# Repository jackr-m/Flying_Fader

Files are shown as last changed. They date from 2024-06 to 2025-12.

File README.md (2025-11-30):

# Flying Faders
## Use Rust Embassy framework to integrate 5 "flying faders" (motorized linear slide potentiometers) as a USB MIDI CC controller

- [Flying Faders](#flying-faders)
   * [Use Rust Embassy framework to integrate 5 "flying faders" (motorized linear slide potentiometers) as a USB MIDI CC controller](#use-rust-embassy-framework-to-integrate-5-flying-faders-motorized-linear-slide-potentiometers-as-a-usb-midi-cc-controller)
   * [Project Overview](#project-overview)
      + [Code](#code)
      + [Mechanical](#mechanical)

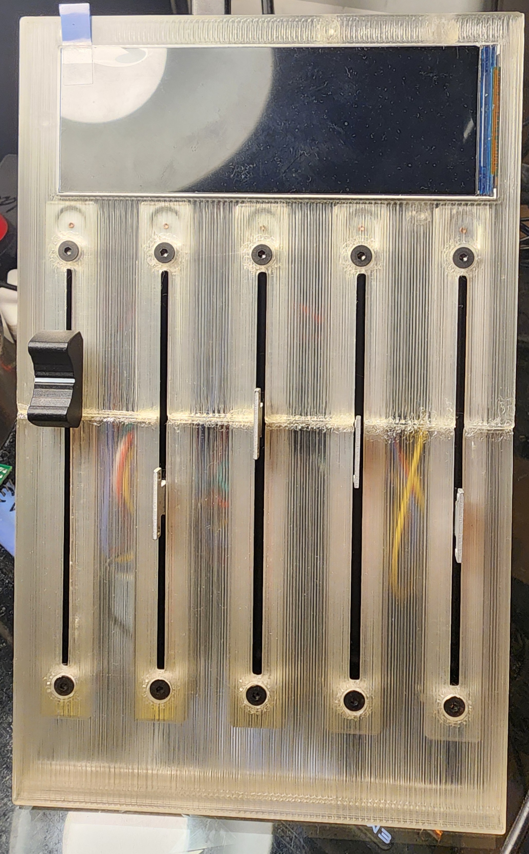
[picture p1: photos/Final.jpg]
Final product


## Project Overview
Use 5 motorized linear slide potentiometers (ALPS SM10002NKA1X-HW1, sold as Adafruit P/N 5466) with a STM32H7 microprocessor programmed using the Rust Embassy framework & HAL.
There is a custom PCB for this project, with the KiCad source in the /CAD directory.
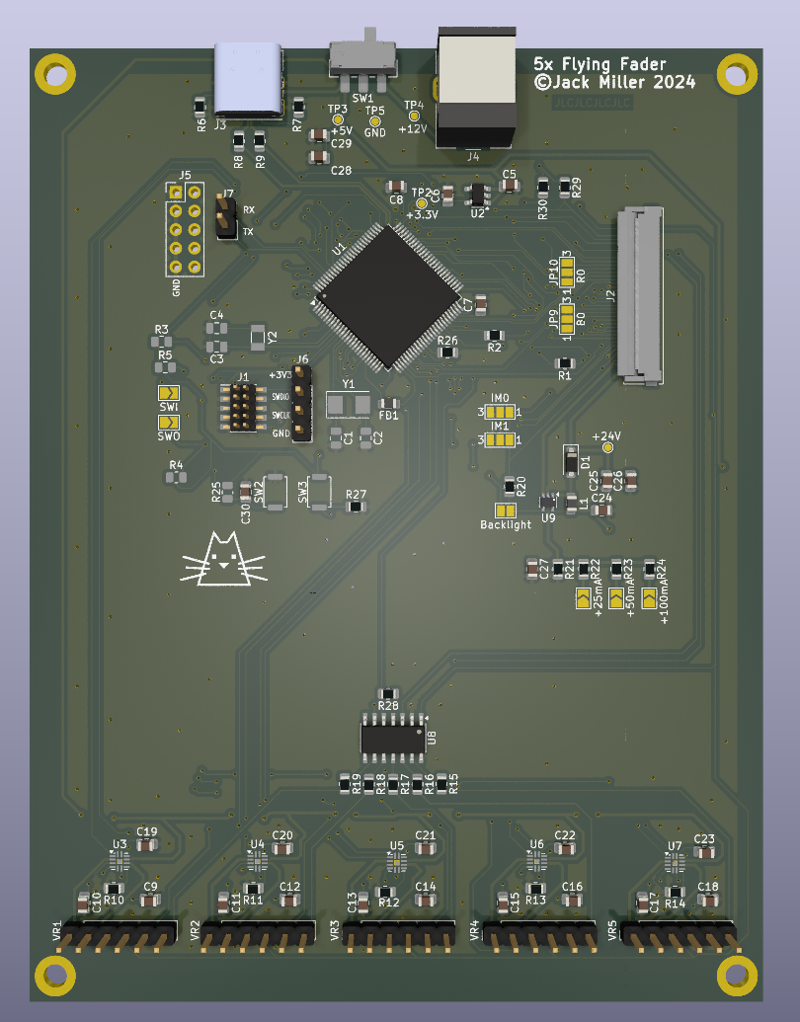
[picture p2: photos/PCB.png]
PCB


### Code
Using the Rust Embassy framework and embassy_stm32 HAL, this has been coded using an asynchronous architecture and should be very portable to nearly any STM32 variant (especially if the screen is not needed).
Code documentation located at: https://jackr-m.github.io/Flying_Fader/flying_fader/

### Mechanical
The casement is 3D printed, and STEP files are provided in the /CAD directory.
In addition, the original Onshape document is available for use or modification at [Onshape](https://cad.onshape.com/documents/5790ae0e6f82956a005dc546/w/d37346e9ef2c1592c912aa6b/e/dacfcc9dc0c38682bf8baa7f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).
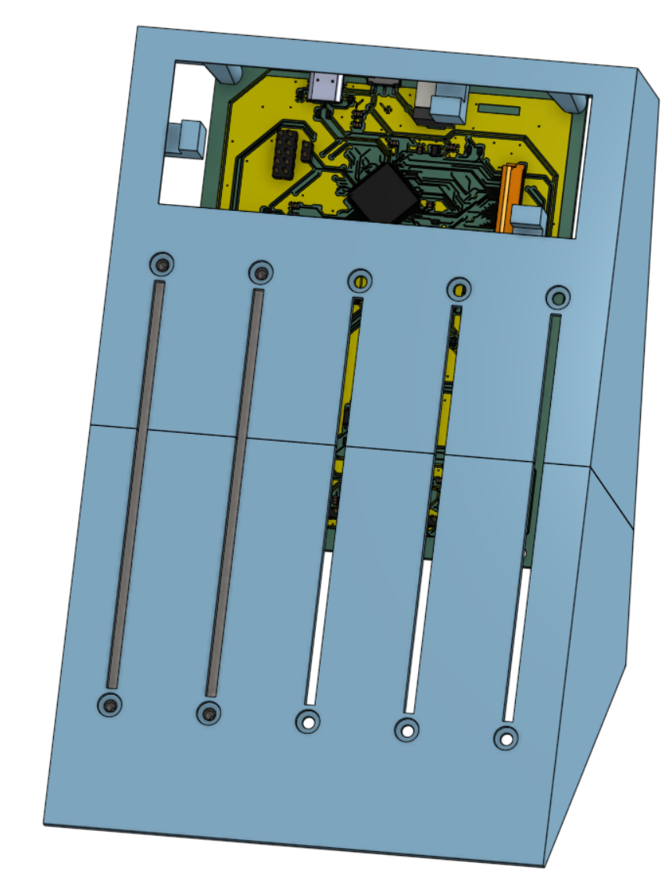
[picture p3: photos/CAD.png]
CAD


Faders:
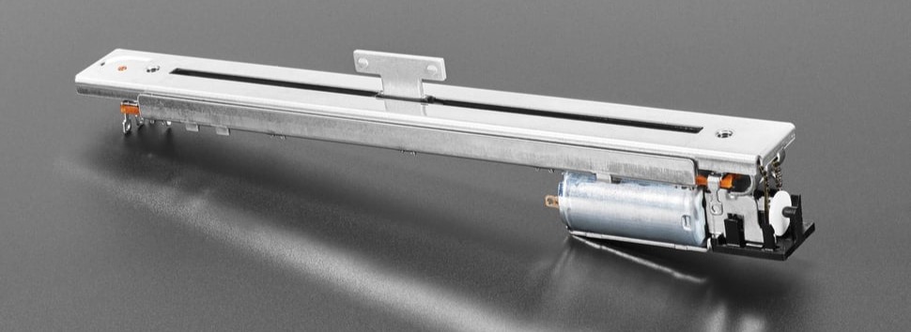
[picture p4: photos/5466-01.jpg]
Fader

https://www.adafruit.com/product/5466

Screen:
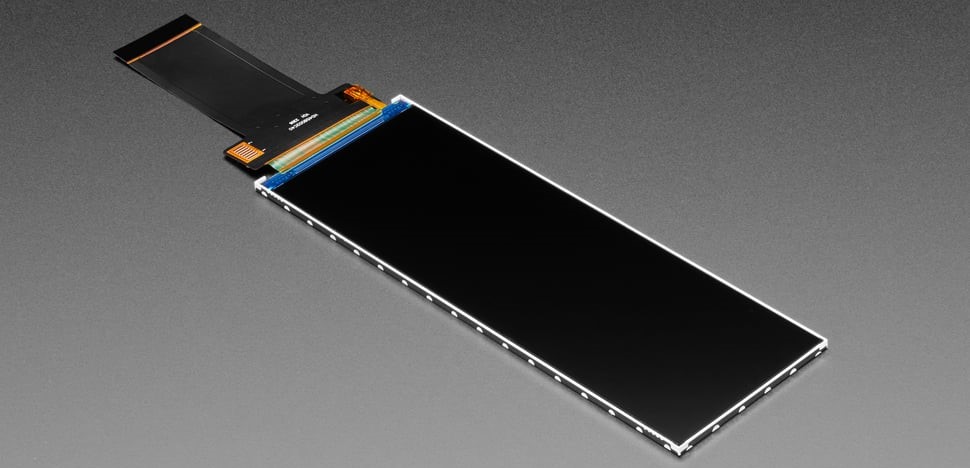
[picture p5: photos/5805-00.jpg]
Screem

https://www.adafruit.com/product/5805

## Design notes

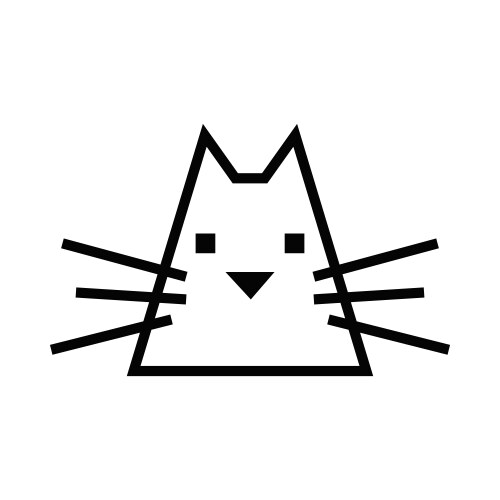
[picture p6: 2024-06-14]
CAD/cat.jpg

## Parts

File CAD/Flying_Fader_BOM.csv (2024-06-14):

Reference | Value | Datasheet | Footprint | Qty | DNP
C1,C2,C3,C4 | C_Small | ~ | Capacitor_SMD:C_0805_2012Metric | 4 | DNP
C5,C6,C25,C26 | 1u | ~ | Capacitor_SMD:C_0805_2012Metric | 4
C7,C8 | 2.2u | ~ | Capacitor_SMD:C_0805_2012Metric | 2
C9,C12,C14,C16,C18,C27,C28,C30 | 0.1u | ~ | Capacitor_SMD:C_0805_2012Metric | 8
C10,C11,C13,C15,C17 | 0.47u | ~ | Capacitor_SMD:C_0805_2012Metric | 5
C19,C20,C21,C22,C23 | 0.1n | ~ | Capacitor_SMD:C_0805_2012Metric | 5
C24,C29 | 10u | ~ | Capacitor_SMD:C_0805_2012Metric | 2
D1 | MBR0540 | http://www.mccsemi.com/up_pdf/MBR0520~MBR0580(SOD123).pdf | Diode_SMD:D_SOD-123 | 1
FB1 | 10uH | ~ | Inductor_SMD:L_0805_2012Metric | 1
J1 | Conn_ARM_JTAG_SWD_10 | http://infocenter.arm.com/help/topic/com.arm.doc.ddi0314h/DDI0314H_coresight_components_trm.pdf | Connector_PinHeader_1.27mm:PinHeader_2x05_P1.27mm_Vertical_SMD | 1
J2 | 40P_FPC_0.5mm | ~ | Connector_FFC-FPC:Omron_XF2M-4015-1A_1x40-1MP_P0.5mm_Horizontal | 1
J3 | USB_C_Receptacle_USB2.0_16P | https://www.usb.org/sites/default/files/documents/usb_type-c.zip | Connector_USB:USB_C_Receptacle_GCT_USB4085 | 1
J4 | Barrel_Jack | ~ | Connector_BarrelJack:BarrelJack_CUI_PJ-063AH_Horizontal | 1
J5 | Conn_02x05_Odd_Even | ~ | Connector_PinHeader_2.54mm:PinHeader_2x05_P2.54mm_Vertical | 1
J6 | Conn_01x04_Pin | ~ | Connector_PinHeader_2.54mm:PinHeader_1x04_P2.54mm_Vertical | 1
J7 | UART4 | ~ | Connector_PinHeader_2.54mm:PinHeader_1x02_P2.54mm_Vertical | 1
L1 | 6.8u | ~ | Inductor_SMD:L_0805_2012Metric | 1
R1,R15,R16,R17,R18,R19,R20,R26,R27 | 10k | ~ | Resistor_SMD:R_0805_2012Metric | 9
R2 | 100 | ~ | Resistor_SMD:R_0805_2012Metric | 1
R3,R4,R5,R25 | 10k | ~ | Resistor_SMD:R_0805_2012Metric | 4 | DNP
R6,R7 | 5.1k | ~ | Resistor_SMD:R_0805_2012Metric | 2
R8,R9 | 0 | ~ | Resistor_SMD:R_0805_2012Metric | 2
R10,R11,R12,R13,R14 | 6.8k | ~ | Resistor_SMD:R_0805_2012Metric | 5
R21,R22 | 8.2 | ~ | Resistor_SMD:R_0805_2012Metric | 2
R23 | 4.3 | ~ | Resistor_SMD:R_0805_2012Metric | 1
R24 | 2 | ~ | Resistor_SMD:R_0805_2012Metric | 1
R28,R29,R30 | 4.7k | ~ | Resistor_SMD:R_0805_2012Metric | 3
SW1 | SW_SPDT | ~ | Button_Switch_SMD:SW_SPDT_CK_JS102011SAQN | 1
SW2 | RESET | ~ | Button_Switch_SMD:SW_Push_SPST_NO_Alps_SKRK | 1
SW3 | BOOT0 | ~ | Button_Switch_SMD:SW_Push_SPST_NO_Alps_SKRK | 1
TP1 | +24V | ~ | TestPoint:TestPoint_Pad_D1.0mm | 1
TP2 | +3.3V | ~ | TestPoint:TestPoint_Pad_D1.0mm | 1
TP3 | +5V | ~ | TestPoint:TestPoint_Pad_D1.0mm | 1
TP4 | +12V | ~ | TestPoint:TestPoint_Pad_D1.0mm | 1
TP5 | GND | ~ | TestPoint:TestPoint_Pad_D1.0mm | 1
U1 | STM32H7A3VITx | https://www.st.com/resource/en/datasheet/stm32h7a3vi.pdf | Package_QFP:LQFP-100_14x14mm_P0.5mm | 1
U2 | MIC5504-3.3YM5 | http://ww1.microchip.com/downloads/en/DeviceDoc/MIC550X.pdf | Package_TO_SOT_SMD:SOT-23-5 | 1
U3,U4,U5,U6,U7 | MP6550GG-Z | MP6550GG-Z | Package_DFN_QFN:LQFN-12-1EP_2x2mm_P0.5mm_EP0.7x0.7mm | 5
U8 | AT42QT1070-S | http://ww1.microchip.com/downloads/en/DeviceDoc/Atmel-9596-AT42-QTouch-BSW-AT42QT1070_Datasheet.pdf | Package_SO:SOIC-14_3.9x8.7mm_P1.27mm | 1
U9 | TPS61169DCKR |  | Package_TO_SOT_SMD:SOT-353_SC-70-5 | 1
VR1,VR2,VR3,VR4,VR5 | SM10002NKA1X-HW1 | https://cdn-shop.adafruit.com/product-files/5466/5466_datasheetSM10001.pdf | Connector_PinHeader_2.54mm:PinHeader_1x06_P2.54mm_Vertical | 5
Y1 | 50MHz | ~ | Crystal:Crystal_SMD_5032-2Pin_5.0x3.2mm | 1 | DNP
Y2 | 32.768kHz | ~ | Crystal:Crystal_SMD_3215-2Pin_3.2x1.5mm | 1 | DNP

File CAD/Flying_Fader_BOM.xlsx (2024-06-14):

Reference | Value | Datasheet | Footprint | Qty | DNP | DigiKey P/N
C1,C2,C3,C4 | C_Small | ~ | Capacitor_SMD:C_0805_2012Metric | 4 | DNP | --
C5,C6,C25,C26 | 1u | ~ | Capacitor_SMD:C_0805_2012Metric | 4 |  | 0805 Book
C7,C8 | 2.2u | ~ | Capacitor_SMD:C_0805_2012Metric | 2 |  | 445-CGA4J1X7R2A225K125ACCT-ND
C9,C12,C14,C16,C18,C27,C28,C30 | 0.1u | ~ | Capacitor_SMD:C_0805_2012Metric | 8 |  | 0805 Book
C10,C11,C13,C15,C17 | 0.47u | ~ | Capacitor_SMD:C_0805_2012Metric | 5 |  | 0805 Book
C19,C20,C21,C22,C23 | 0.1n | ~ | Capacitor_SMD:C_0805_2012Metric | 5 |  | 0805 Book
C24,C29 | 10u | ~ | Capacitor_SMD:C_0805_2012Metric | 2 |  | 490-GRJ21BR61E106KE01KCT-ND
D1 | MBR0540 | http://www.mccsemi.com/up_pdf/MBR0520~MBR0580(SOD123).pdf | Diode_SMD:D_SOD-123 | 1 |  | 1655-MBR0540CT-ND
FB1 | 10uH | ~ | Inductor_SMD:L_0805_2012Metric | 1 |  | 553-2392-1-ND
J1 | Conn_ARM_JTAG_SWD_10 | http://infocenter.arm.com/help/topic/com.arm.doc.ddi0314h/DDI0314H_coresight_components_trm.pdf | Connector_PinHeader_1.27mm:PinHeader_2x05_P1.27mm_Vertical_SMD | 1 | DNP | --
J2 | 40P_FPC_0.5mm | ~ | Connector_FFC-FPC:Omron_XF2M-4015-1A_1x40-1MP_P0.5mm_Horizontal | 1 |  | OR729CT-ND
J3 | USB_C_Receptacle_USB2.0_16P | https://www.usb.org/sites/default/files/documents/usb_type-c.zip | Connector_USB:USB_C_Receptacle_GCT_USB4085 | 1 |  | 2073-USB4085-GF-ACT-ND
J4 | Barrel_Jack | ~ | Connector_BarrelJack:BarrelJack_CUI_PJ-063AH_Horizontal | 1 |  | CP-063AH-ND
J5 | Conn_02x05_Odd_Even | ~ | Connector_PinHeader_2.54mm:PinHeader_2x05_P2.54mm_Vertical | 1 | DNP
J6 | Conn_01x04_Pin | ~ | Connector_PinHeader_2.54mm:PinHeader_1x04_P2.54mm_Vertical | 1 |  | --
J7 | UART4 | ~ | Connector_PinHeader_2.54mm:PinHeader_1x02_P2.54mm_Vertical | 1 |  | --
L1 | 6.8u | ~ | Inductor_SMD:L_0805_2012Metric | 1 |  | 445-6761-1-ND
R1,R15,R16,R17,R18,R19,R20,R26,R27 | 10k | ~ | Resistor_SMD:R_0805_2012Metric | 9 |  | 0805 Book
R2 | 100 | ~ | Resistor_SMD:R_0805_2012Metric | 1 |  | 0805 Book
R3,R4,R5,R25 | 10k | ~ | Resistor_SMD:R_0805_2012Metric | 4 | DNP | 0805 Book
R6,R7 | 5.1k | ~ | Resistor_SMD:R_0805_2012Metric | 2 |  | 0805 Book
R8,R9 | 0 | ~ | Resistor_SMD:R_0805_2012Metric | 2 |  | 0805 Book
R10,R11,R12,R13,R14 | 6.8k | ~ | Resistor_SMD:R_0805_2012Metric | 5 |  | 0805 Book
R21,R22 | 8.2 | ~ | Resistor_SMD:R_0805_2012Metric | 2 |  | 0805 Book
R23 | 4.3 | ~ | Resistor_SMD:R_0805_2012Metric | 1 |  | 0805 Book
R24 | 2 | ~ | Resistor_SMD:R_0805_2012Metric | 1 |  | 0805 Book
R28,R29,R30 | 4.7k | ~ | Resistor_SMD:R_0805_2012Metric | 3 |  | 311-4.7KARCT-ND
SW1 | SW_SPDT | ~ | Button_Switch_SMD:SW_SPDT_CK_JS102011SAQN | 1 |  | 401-1999-1-ND
SW2 | RESET | ~ | Button_Switch_SMD:SW_Push_SPST_NO_Alps_SKRK | 1 |  | 4809-SKRKAHE020CT-ND
SW3 | BOOT0 | ~ | Button_Switch_SMD:SW_Push_SPST_NO_Alps_SKRK | 1 |  | 4809-SKRKAHE020CT-ND
TP1 | +24V | ~ | TestPoint:TestPoint_Pad_D1.0mm | 1 |  | --
TP2 | +3.3V | ~ | TestPoint:TestPoint_Pad_D1.0mm | 1 |  | --
TP3 | +5V | ~ | TestPoint:TestPoint_Pad_D1.0mm | 1 |  | --
TP4 | +12V | ~ | TestPoint:TestPoint_Pad_D1.0mm | 1 |  | --
TP5 | GND | ~ | TestPoint:TestPoint_Pad_D1.0mm | 1 |  | --
U1 | STM32H7A3VITx | https://www.st.com/resource/en/datasheet/stm32h7a3vi.pdf | Package_QFP:LQFP-100_14x14mm_P0.5mm | 1 |  | 497-STM32H7A3VIT6-ND
U2 | MIC5504-3.3YM5 | http://ww1.microchip.com/downloads/en/DeviceDoc/MIC550X.pdf | Package_TO_SOT_SMD:SOT-23-5 | 1 |  | 576-4764-1-ND
U3,U4,U5,U6,U7 | MP6550GG-Z | MP6550GG-Z | Package_DFN_QFN:LQFN-12-1EP_2x2mm_P0.5mm_EP0.7x0.7mm | 5 |  | 1589-MP6550GG-ZCT-ND
U8 | AT42QT1070-S | http://ww1.microchip.com/downloads/en/DeviceDoc/Atmel-9596-AT42-QTouch-BSW-AT42QT1070_Datasheet.pdf | Package_SO:SOIC-14_3.9x8.7mm_P1.27mm | 1 |  | AT42QT1070-SSURCT-ND
U9 | TPS61169DCKR |  | Package_TO_SOT_SMD:SOT-353_SC-70-5 | 1 |  | 296-40821-1-ND
VR1,VR2,VR3,VR4,VR5 | SM10002NKA1X-HW1 | https://cdn-shop.adafruit.com/product-files/5466/5466_datasheetSM10001.pdf | Connector_PinHeader_2.54mm:PinHeader_1x06_P2.54mm_Vertical | 5 |  | 1528-5466-ND | 1528-5741-ND
Y1 | 50MHz | ~ | Crystal:Crystal_SMD_5032-2Pin_5.0x3.2mm | 1 | DNP | 50-ECS-500-CDX-2166CT-ND
Y2 | 32.768kHz | ~ | Crystal:Crystal_SMD_3215-2Pin_3.2x1.5mm | 1 | DNP | 50-ECS-.327-6-34B-C-CT-ND

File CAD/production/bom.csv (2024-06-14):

Designator | Footprint | Quantity | Value | LCSC Part #
C1, C2, C3, C4 | 0805 | 4 | C_Small
C10, C11, C13, C15, C17 | 0805 | 5 | 0.47u
C12, C14, C16, C18, C27, C28, C30, C9 | 0805 | 8 | 0.1u
C19, C20, C21, C22, C23 | 0805 | 5 | 0.1n
C24, C29 | 0805 | 2 | 10u
C25, C26, C5, C6 | 0805 | 4 | 1u
C7, C8 | 0805 | 2 | 2.2u
D1 | D_SOD-123 | 1 | MBR0540
FB1 | 0805 | 1 | 10uH
J1 | PinHeader_2x05_P1.27mm_Vertical_SMD | 1 | Conn_ARM_JTAG_SWD_10
J2 | Omron_XF2M-4015-1A_1x40-1MP_P0.5mm_Horizontal | 1 | 40P_FPC_0.5mm
J3 | USB_C_Receptacle_GCT_USB4085 | 1 | USB_C_Receptacle_USB2.0_16P
J4 | BarrelJack_CUI_PJ-063AH_Horizontal | 1 | Barrel_Jack
J5 | PinHeader_2x05_P2.54mm_Vertical | 1 | Conn_02x05_Odd_Even
J6 | PinHeader_1x04_P2.54mm_Vertical | 1 | Conn_01x04_Pin
J7 | PinHeader_1x02_P2.54mm_Vertical | 1 | UART4
L1 | 0805 | 1 | 6.8u
R1, R15, R16, R17, R18, R19, R20, R25, R26, R27, R3, R4, R5 | 0805 | 13 | 10k
R10, R11, R12, R13, R14 | 0805 | 5 | 6.8k
R2 | 0805 | 1 | 100
R21, R22 | 0805 | 2 | 8.2
R23 | 0805 | 1 | 4.3
R24 | 0805 | 1 | 2
R28, R29, R30 | 0805 | 3 | 4.7k
R6, R7 | 0805 | 2 | 5.1k
R8, R9 | 0805 | 2 | 0
SW1 | SW_SPDT_CK_JS102011SAQN | 1 | SW_SPDT
SW2 | SW_Push_SPST_NO_Alps_SKRK | 1 | RESET
SW3 | SW_Push_SPST_NO_Alps_SKRK | 1 | BOOT0
TP1 | TestPoint_Pad_D1.0mm | 1 | +24V
TP2 | TestPoint_Pad_D1.0mm | 1 | +3.3V
TP3 | TestPoint_Pad_D1.0mm | 1 | +5V
TP4 | TestPoint_Pad_D1.0mm | 1 | +12V
TP5 | TestPoint_Pad_D1.0mm | 1 | GND
U1 | LQFP-100_14x14mm_P0.5mm | 1 | STM32H7A3VITx
U2 | SOT-23-5 | 1 | MIC5504-3.3YM5
U3, U4, U5, U6, U7 | LQFN-12-1EP_2x2mm_P0.5mm_EP0.7x0.7mm | 5 | MP6550GG-Z
U8 | SOIC-14_3.9x8.7mm_P1.27mm | 1 | AT42QT1070-S
U9 | SOT-353_SC-70-5 | 1 | TPS61169DCKR
VR1, VR2, VR3, VR4, VR5 | PinHeader_1x06_P2.54mm_Vertical | 5 | SM10002NKA1X-HW1
Y1 | Crystal_SMD_5032-2Pin_5.0x3.2mm | 1 | 50MHz
Y2 | Crystal_SMD_3215-2Pin_3.2x1.5mm | 1 | 32.768kHz

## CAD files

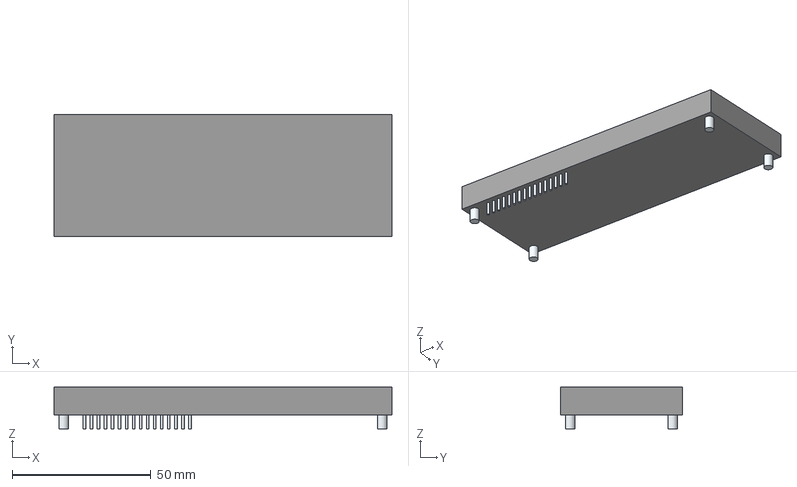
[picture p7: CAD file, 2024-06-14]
CAD/LIB_NHD-0216SZW-BG5/NHD-0216SZW-BG5/3D/NHD-0216SZW-BG5.stp
122.0 x 44.0 x 15.1 mm
Leads x 20

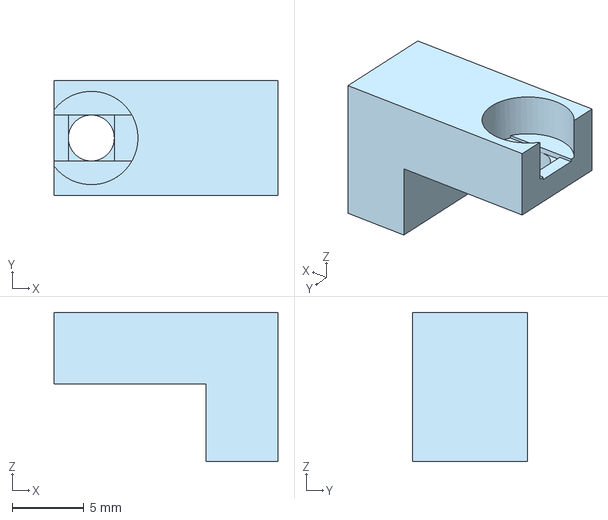
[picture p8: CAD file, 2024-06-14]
CAD/Screen Clamp Short.step
15.6 x 8.00 x 10.4 mm

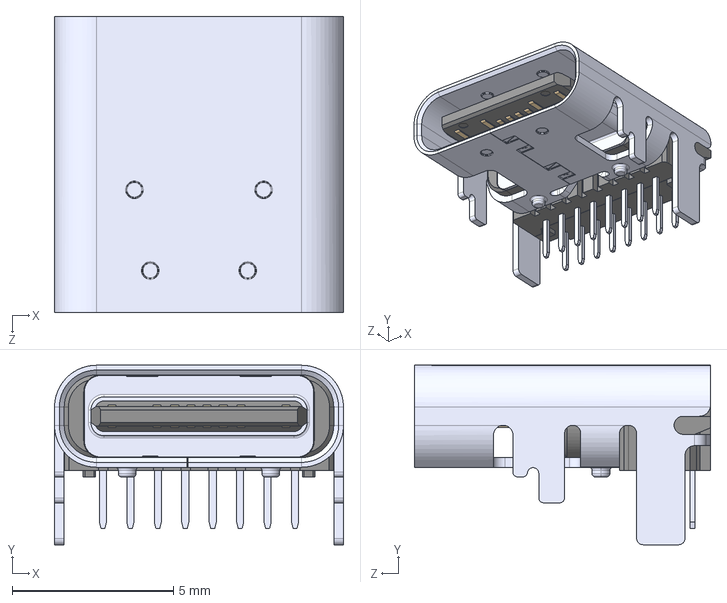
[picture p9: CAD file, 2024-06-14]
CAD/USB4085_GF_A/USB4085-GF-A.step
8.95 x 5.56 x 9.17 mm

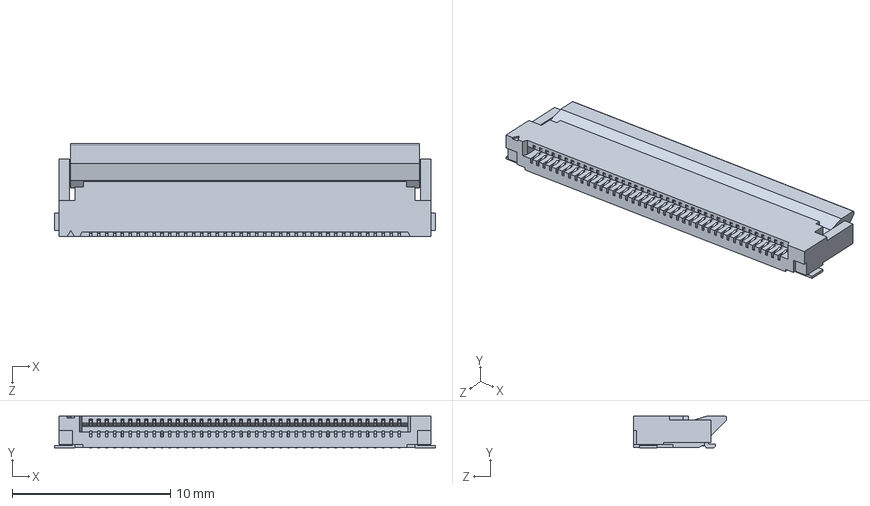
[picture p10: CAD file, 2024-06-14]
CAD/XF2M_4015_1A/XF2M_4015_1A.step
24.1 x 2.00 x 5.90 mm

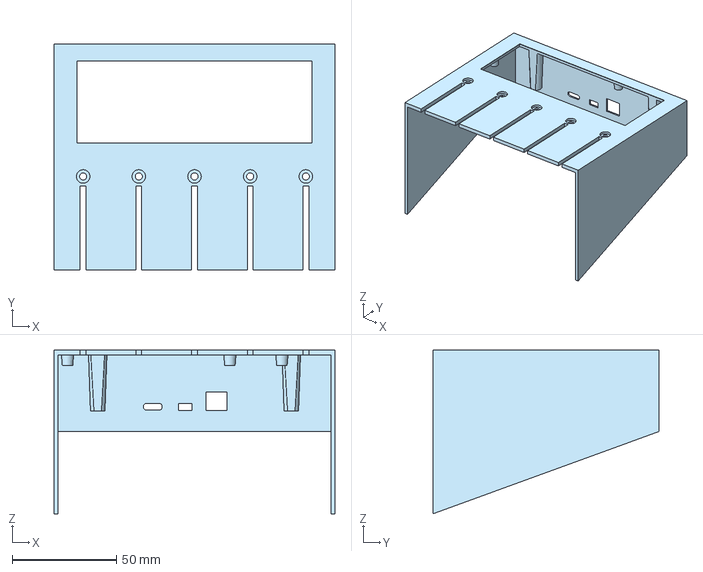
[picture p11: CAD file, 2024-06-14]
CAD/Top Panel Upper.step
135.0 x 108.6 x 78.6 mm

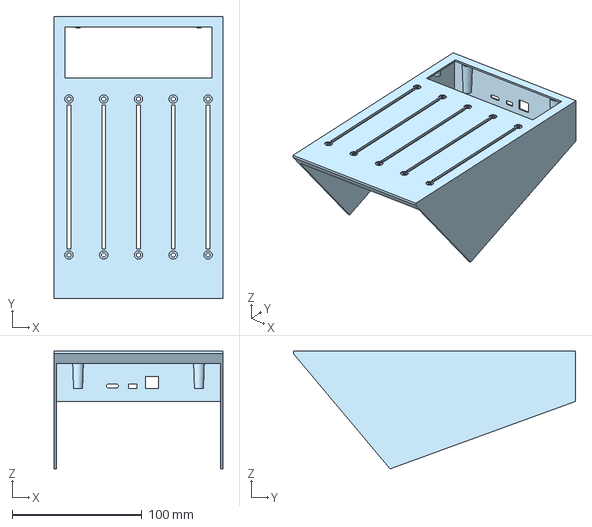
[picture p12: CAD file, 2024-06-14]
CAD/Top Panel.step
130.0 x 217.0 x 90.6 mm

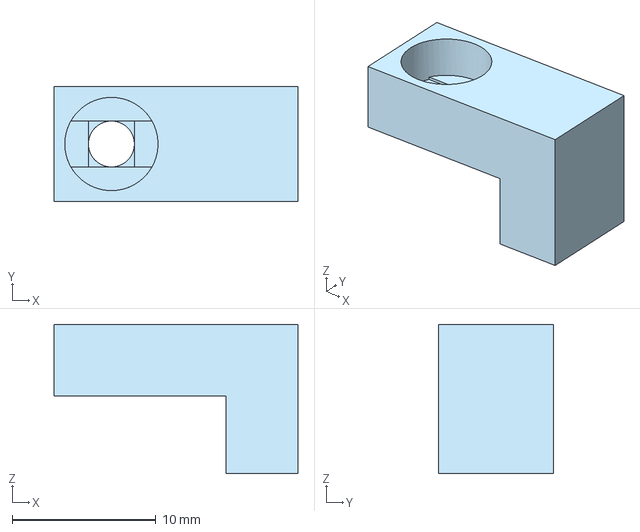
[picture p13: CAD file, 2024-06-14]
CAD/Screen Clamp.step
17.0 x 8.00 x 10.4 mm

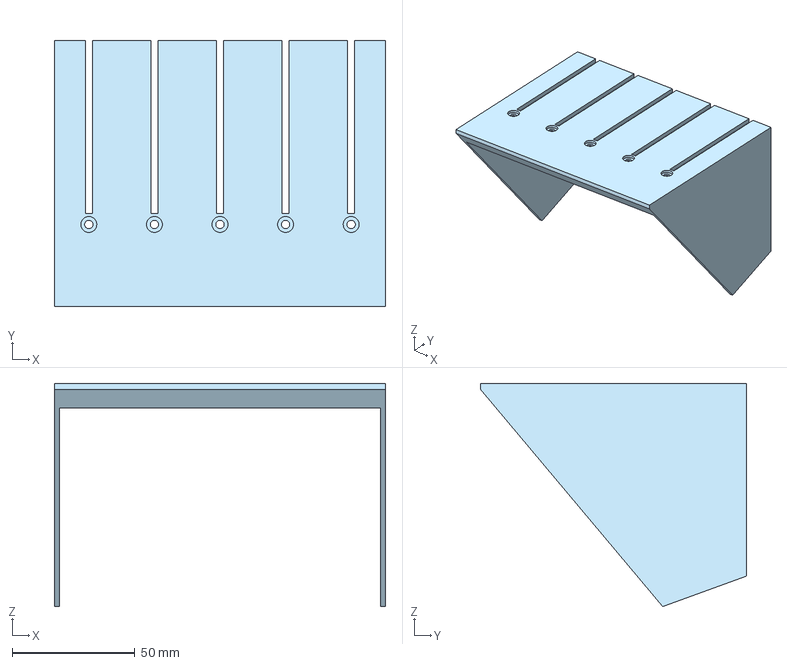
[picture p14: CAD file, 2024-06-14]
CAD/Top Panel Lower.step
135.0 x 108.6 x 91.0 mm

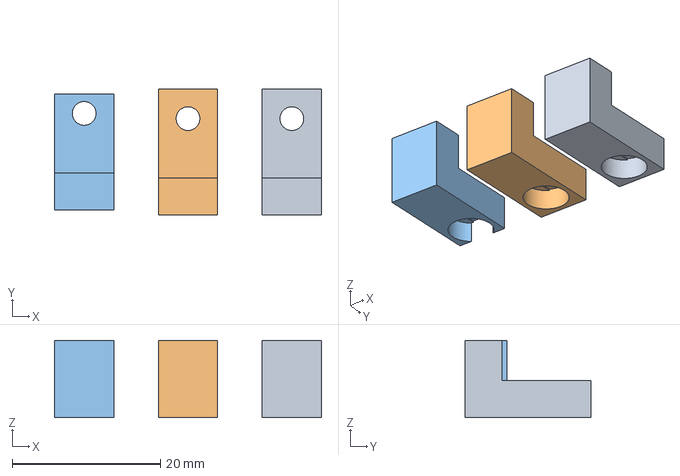
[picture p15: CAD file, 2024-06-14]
CAD/Screen Clamps.3mf
36.0 x 17.0 x 10.4 mm
Screen Clamp
Screen Clamp Short

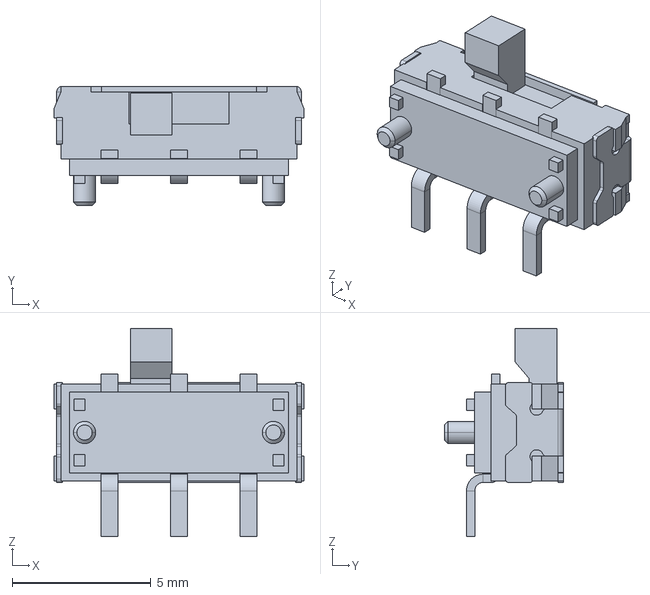
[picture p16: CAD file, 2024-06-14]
CAD/JS102011SAQN/JS102011SAQN.step
9.00 x 4.30 x 7.50 mm

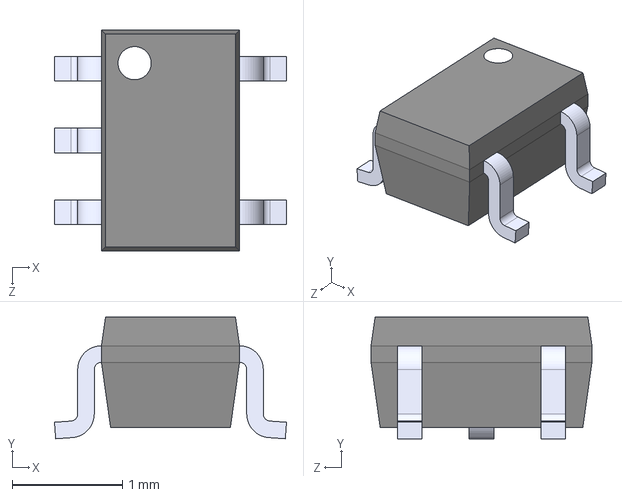
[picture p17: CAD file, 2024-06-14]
CAD/TPS61169DCKR/TPS61169DCKR.step
2.10 x 1.10 x 2.00 mm

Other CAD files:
CAD/LIB_NHD-0216SZW-BG5/NHD-0216SZW-BG5/Allegro/nhd0216szwbg5.psm
CAD/LIB_NHD-0216SZW-BG5/NHD-0216SZW-BG5/DEHDL/nhd_0216szw_bg5/chips/chips.prt
CAD/Top Panel Lower.3mf
CAD/Top Panel Upper.3mf
CAD/Top Panel.3mf

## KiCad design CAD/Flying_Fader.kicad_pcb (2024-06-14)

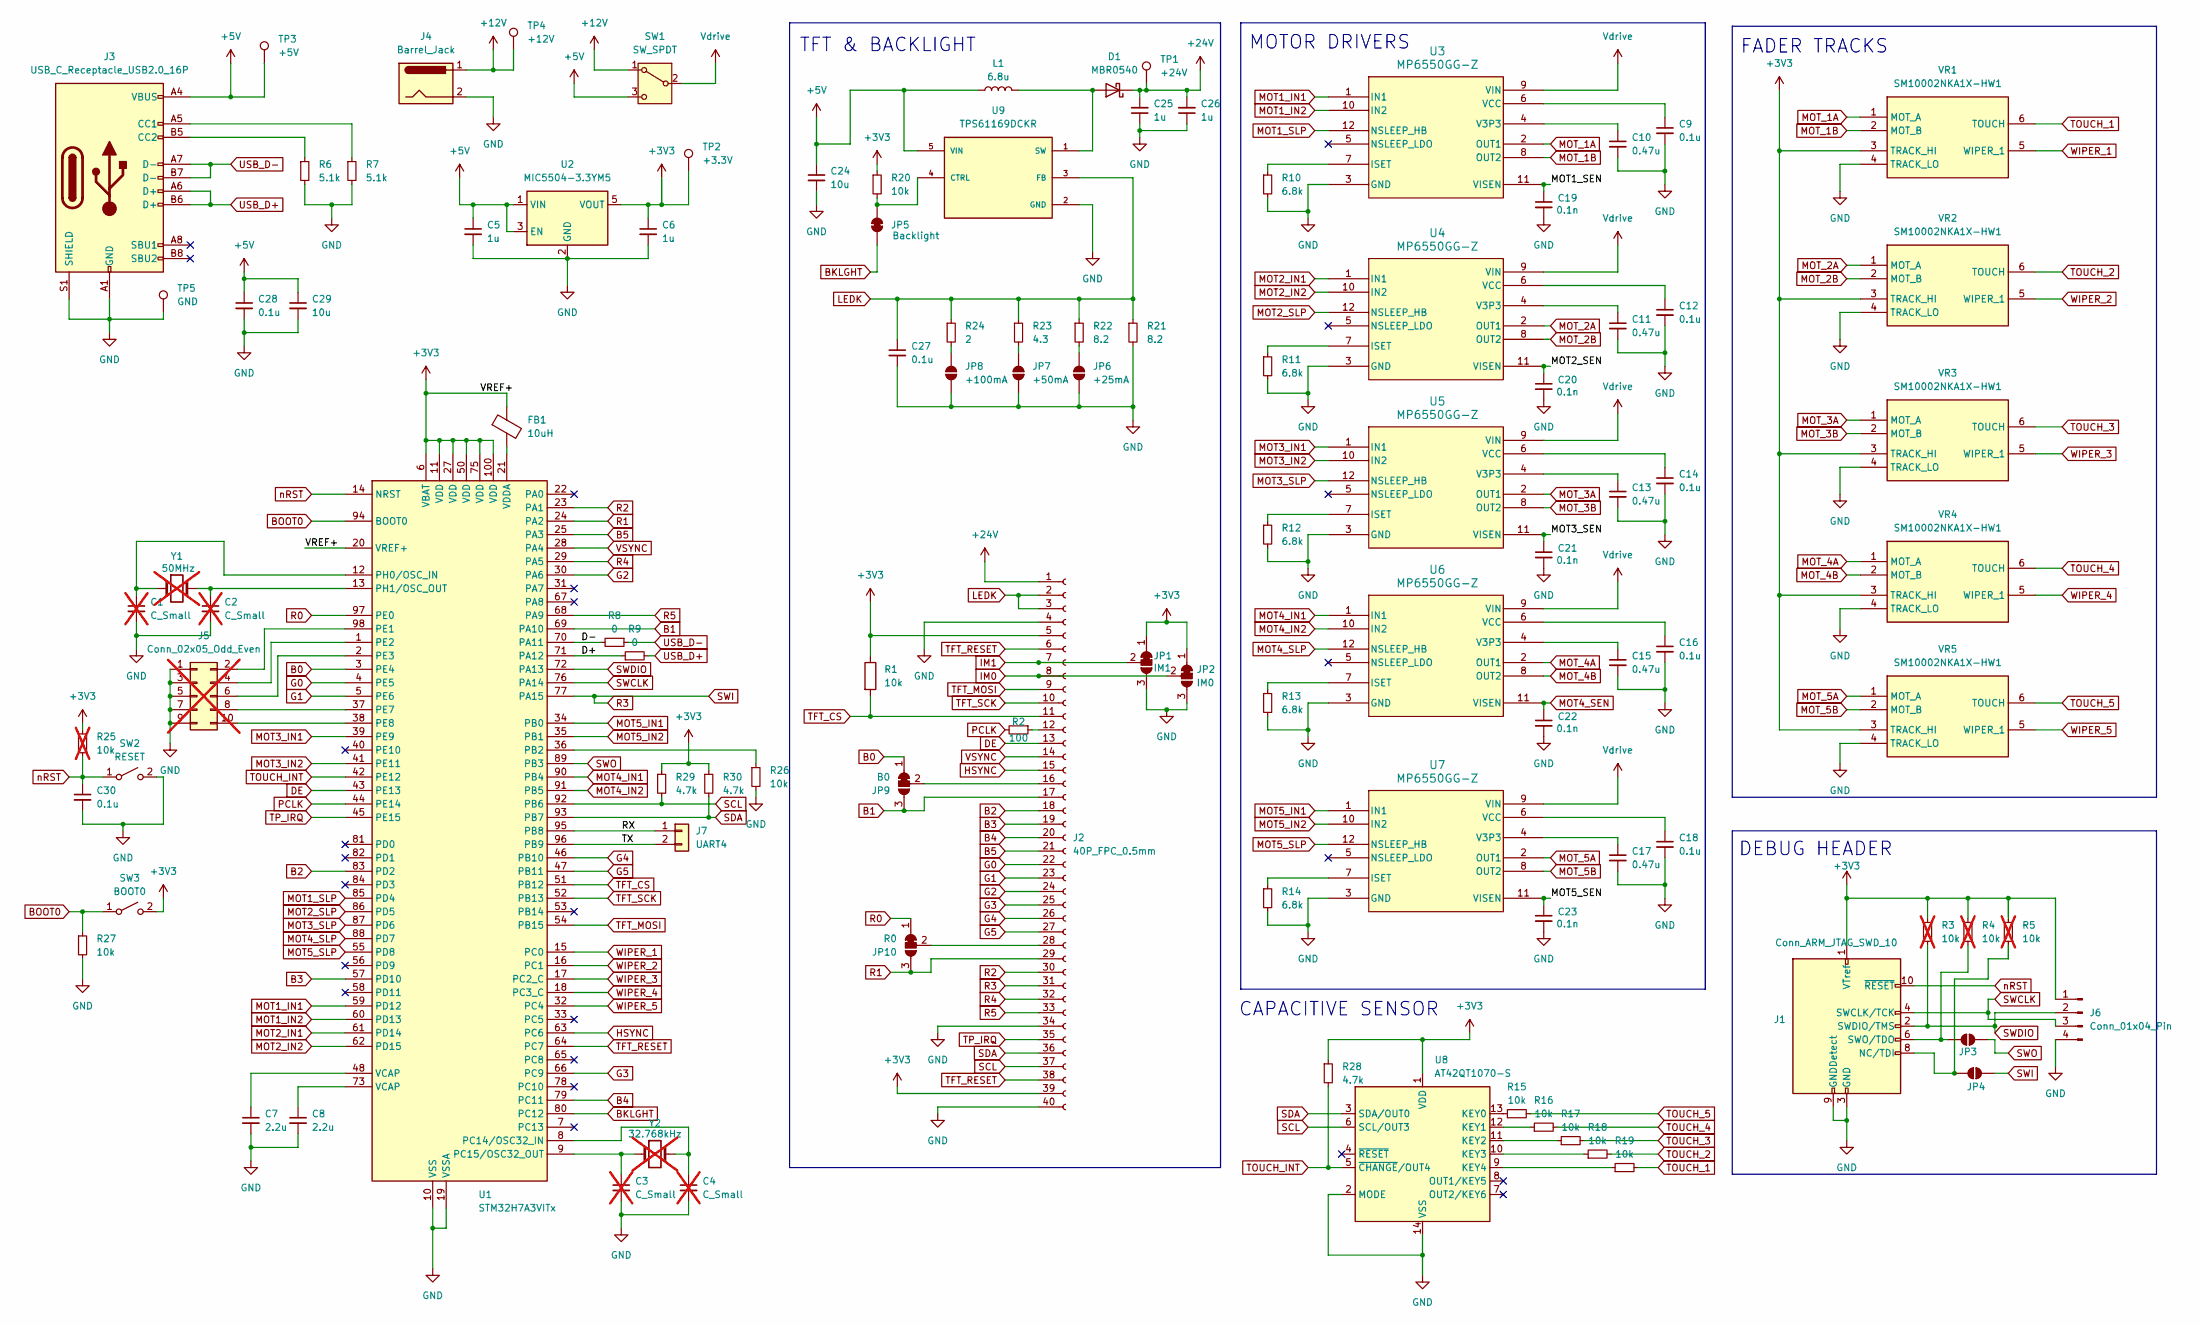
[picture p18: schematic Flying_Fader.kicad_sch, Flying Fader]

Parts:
C1, C2, C3, C4: C_Small; C_0805_2012Metric; not fitted
C5, C6, C25, C26: 1u; C_0805_2012Metric
C7, C8: 2.2u; C_0805_2012Metric
C9, C12, C14, C16, C18, C27, C28, C30: 0.1u; C_0805_2012Metric
C10, C11, C13, C15, C17: 0.47u; C_0805_2012Metric
C19, C20, C21, C22, C23: 0.1n; C_0805_2012Metric
C24, C29: 10u; C_0805_2012Metric
D1: MBR0540; D_SOD-123
FB1: 10uH; L_0805_2012Metric
J1: Conn_ARM_JTAG_SWD_10; PinHeader_2x05_P1.27mm_Vertical_SMD
J2: 40P_FPC_0.5mm; Omron_XF2M-4015-1A_1x40-1MP_P0.5mm_Horizontal
J3: USB_C_Receptacle_USB2.0_16P; USB_C_Receptacle_GCT_USB4085
J4: Barrel_Jack; BarrelJack_CUI_PJ-063AH_Horizontal
J5: Conn_02x05_Odd_Even; PinHeader_2x05_P2.54mm_Vertical; not fitted
J6: Conn_01x04_Pin; PinHeader_1x04_P2.54mm_Vertical
J7: UART4; PinHeader_1x02_P2.54mm_Vertical
JP1: IM1; SolderJumper-3_P1.3mm_Bridged12_Pad1.0x1.5mm_NumberLabels
JP2: IM0; SolderJumper-3_P1.3mm_Bridged12_Pad1.0x1.5mm_NumberLabels
JP3: SWO; SolderJumper-2_P1.3mm_Open_TrianglePad1.0x1.5mm
JP4: SWI; SolderJumper-2_P1.3mm_Open_TrianglePad1.0x1.5mm
JP5: Backlight; SolderJumper-2_P1.3mm_Bridged_Pad1.0x1.5mm
JP6: +25mA; SolderJumper-2_P1.3mm_Open_TrianglePad1.0x1.5mm
JP7: +50mA; SolderJumper-2_P1.3mm_Open_TrianglePad1.0x1.5mm
JP8: +100mA; SolderJumper-2_P1.3mm_Open_TrianglePad1.0x1.5mm
JP9: B0; SolderJumper-3_P1.3mm_Bridged12_Pad1.0x1.5mm_NumberLabels
JP10: R0; SolderJumper-3_P1.3mm_Bridged12_Pad1.0x1.5mm_NumberLabels
L1: 6.8u; L_0805_2012Metric
R1, R15, R16, R17, R18, R19, R20, R26, R27: 10k; R_0805_2012Metric
R2: 100; R_0805_2012Metric
R3, R4, R5, R25: 10k; R_0805_2012Metric; not fitted
R6, R7: 5.1k; R_0805_2012Metric
R8, R9: 0; R_0805_2012Metric
R10, R11, R12, R13, R14: 6.8k; R_0805_2012Metric
R21, R22: 8.2; R_0805_2012Metric
R23: 4.3; R_0805_2012Metric
R24: 2; R_0805_2012Metric
R28, R29, R30: 4.7k; R_0805_2012Metric
SW1: SW_SPDT; SW_SPDT_CK_JS102011SAQN
SW2: RESET; SW_Push_SPST_NO_Alps_SKRK
SW3: BOOT0; SW_Push_SPST_NO_Alps_SKRK
TP1: +24V; TestPoint_Pad_D1.0mm
TP2: +3.3V; TestPoint_Pad_D1.0mm
TP3: +5V; TestPoint_Pad_D1.0mm
TP4: +12V; TestPoint_Pad_D1.0mm
TP5: GND; TestPoint_Pad_D1.0mm
U1: STM32H7A3VITx; LQFP-100_14x14mm_P0.5mm
U2: MIC5504-3.3YM5; SOT-23-5
U3, U4, U5, U6, U7: MP6550GG-Z; LQFN-12-1EP_2x2mm_P0.5mm_EP0.7x0.7mm
U8: AT42QT1070-S; SOIC-14_3.9x8.7mm_P1.27mm
U9: TPS61169DCKR; SOT-353_SC-70-5; PARTREV A
VR1, VR2, VR3, VR4, VR5: SM10002NKA1X-HW1; PinHeader_1x06_P2.54mm_Vertical; Manufacturer_Part_Number SM10002NKA1X-HW1
Y1: 50MHz; Crystal_SMD_5032-2Pin_5.0x3.2mm; not fitted
Y2: 32.768kHz; Crystal_SMD_3215-2Pin_3.2x1.5mm; not fitted

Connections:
+3V3: C6.1, FB1.1, J1.1 (VTref), J2.5, J2.39, J6.1, JP1.1 (A), JP2.1 (A), R1.1, R3.1, R4.1, R5.1, R20.1, R25.1, R28.1, R29.1, R30.1, SW3.2 (B), TP2.1, U1.6 (VBAT), U1.11 (VDD), U1.20 (VREF+), U1.27 (VDD), U1.50 (VDD), U1.75 (VDD), U1.100 (VDD), U2.5 (VOUT), U8.1 (VDD), VR1.3 (TRACK_HI), VR2.3 (TRACK_HI), VR3.3 (TRACK_HI), VR4.3 (TRACK_HI), VR5.3 (TRACK_HI)
+5V: C5.1, C24.1, C28.1, C29.1, J3.A4 (VBUS), J3.A9 (VBUS), J3.B4 (VBUS), J3.B9 (VBUS), L1.1, SW1.3 (C), TP3.1, U2.1 (VIN), U2.3 (EN), U9.5 (VIN)
+12V: J4.1, SW1.1 (A), TP4.1
+24V: C25.2, C26.2, D1.1 (K), J2.1, TP1.1
/D+: R9.1, U1.71 (PA12)
/D-: R8.2, U1.70 (PA11)
/MOT1_SEN: C19.1, U3.11 (VISEN)
/MOT2_SEN: C20.1, U4.11 (VISEN)
/MOT3_SEN: C21.1, U5.11 (VISEN)
/MOT5_SEN: C23.1, U7.11 (VISEN)
/RX: J7.1, U1.95 (PB8)
/TX: J7.2, U1.96 (PB9)
B0: JP9.1 (A), U1.3 (PE4)
B1: J2.17, JP9.3 (B), U1.69 (PA10)
B2: J2.18, U1.83 (PD2)
B3: J2.19, U1.57 (PD10)
B4: J2.20, U1.79 (PC11)
B5: J2.21, U1.25 (PA3)
BKLGHT: JP5.1 (A), U1.80 (PC12)
BOOT0: R27.1, SW3.1 (A), U1.94 (BOOT0)
DE: J2.13, U1.43 (PE13)
G0: J2.22, U1.4 (PE5)
G1: J2.23, U1.5 (PE6)
G2: J2.24, U1.30 (PA6)
G3: J2.25, U1.66 (PC9)
G4: J2.26, U1.46 (PB10)
G5: J2.27, U1.47 (PB11)
GND: C1.2, C2.2, C3.2, C4.2, C5.2, C6.2, C7.2, C8.2, C9.2, C10.2, C11.2, C12.2, C13.2, C14.2, C15.2, C16.2, C17.2, C18.2, C19.2, C20.2, C21.2, C22.2, C23.2, C24.2, C25.1, C26.1, C27.2, C28.2, C29.2, C30.2, J1.3 (GND), J1.5 (GND), J1.9 (GNDDetect), J2.4, J2.34, J2.40, J3.A1 (GND), J3.A12 (GND), J3.B1 (GND), J3.B12 (GND), J3.S1 (SHIELD), J4.2, J5.1, J5.3, J5.5, J5.7, J5.9, J6.4, JP1.3 (B), JP2.3 (B), JP6.1 (A), JP7.1 (A), JP8.1 (A), R6.2, R7.2, R10.2, R11.2, R12.2, R13.2, R14.2, R21.2, R26.2, R27.2, SW2.2 (B), TP5.1, U1.10 (VSS), U1.19 (VSSA), U1.26 (VSS), U1.49 (VSS), U1.74 (VSS), U1.99 (VSS), U2.2 (GND), U3.3 (GND), U4.3 (GND), U5.3 (GND), U6.3 (GND), U7.3 (GND), U8.2 (MODE), U8.14 (VSS), U9.2 (GND), VR1.4 (TRACK_LO), VR2.4 (TRACK_LO), VR3.4 (TRACK_LO), VR4.4 (TRACK_LO), VR5.4 (TRACK_LO)
HSYNC: J2.15, U1.63 (PC6)
IM0: J2.8, JP2.2 (C)
IM1: J2.7, JP1.2 (C)
LEDK: C27.1, J2.2, J2.3, R21.1, R22.1, R23.1, R24.1, U9.3 (FB)
MOT1_IN1: U1.59 (PD12), U3.1 (IN1)
MOT1_IN2: U1.60 (PD13), U3.10 (IN2)
MOT1_SLP: U1.85 (PD4), U3.12 (NSLEEP_HB)
MOT2_IN1: U1.61 (PD14), U4.1 (IN1)
MOT2_IN2: U1.62 (PD15), U4.10 (IN2)
MOT2_SLP: U1.86 (PD5), U4.12 (NSLEEP_HB)
MOT3_IN1: U1.39 (PE9), U5.1 (IN1)
MOT3_IN2: U1.41 (PE11), U5.10 (IN2)
MOT3_SLP: U1.87 (PD6), U5.12 (NSLEEP_HB)
MOT4_IN1: U1.90 (PB4), U6.1 (IN1)
MOT4_IN2: U1.91 (PB5), U6.10 (IN2)
MOT4_SEN: C22.1, U6.11 (VISEN)
MOT4_SLP: U1.88 (PD7), U6.12 (NSLEEP_HB)
MOT5_IN1: U1.34 (PB0), U7.1 (IN1)
MOT5_IN2: U1.35 (PB1), U7.10 (IN2)
MOT5_SLP: U1.55 (PD8), U7.12 (NSLEEP_HB)
MOT_1A: U3.2 (OUT1), VR1.1 (MOT_A)
MOT_1B: U3.8 (OUT2), VR1.2 (MOT_B)
MOT_2A: U4.2 (OUT1), VR2.1 (MOT_A)
MOT_2B: U4.8 (OUT2), VR2.2 (MOT_B)
MOT_3A: U5.2 (OUT1), VR3.1 (MOT_A)
MOT_3B: U5.8 (OUT2), VR3.2 (MOT_B)
MOT_4A: U6.2 (OUT1), VR4.1 (MOT_A)
MOT_4B: U6.8 (OUT2), VR4.2 (MOT_B)
MOT_5A: U7.2 (OUT1), VR5.1 (MOT_A)
MOT_5B: U7.8 (OUT2), VR5.2 (MOT_B)
unnamed: C7.1, U1.48 (VCAP)
unnamed: C8.1, U1.73 (VCAP)
unnamed: D1.2 (A), L1.2, U9.1 (SW)
unnamed: J1.8 (NC/TDI), JP4.1 (A), R5.2
unnamed: J1.6 (SWO/TDO), JP3.1 (A), R4.2
unnamed: J2.12, R2.1
unnamed: J2.16, JP9.2 (C)
unnamed: J2.28, JP10.2 (C)
unnamed: J3.A5 (CC1), R7.1
unnamed: J3.B5 (CC2), R6.1
unnamed: J5.2, U1.98 (PE1)
unnamed: J5.4, U1.1 (PE2)
unnamed: J5.6, U1.2 (PE3)
unnamed: J5.8, U1.37 (PE7)
unnamed: J5.10, U1.38 (PE8)
unnamed: JP5.2 (B), R20.2, U9.4 (CTRL)
unnamed: JP6.2 (B), R22.2
unnamed: JP7.2 (B), R23.2
unnamed: JP8.2 (B), R24.2
unnamed: R26.1, U1.36 (PB2)
unnamed: C4.1, U1.8 (PC14/OSC32_IN), Y2.2
unnamed: C3.1, U1.9 (PC15/OSC32_OUT), Y2.1
unnamed: C1.1, U1.12 (PH0/OSC_IN), Y1.1
unnamed: C2.1, U1.13 (PH1/OSC_OUT), Y1.2
unnamed: FB1.2, U1.21 (VDDA)
unnamed: R10.1, U3.7 (ISET)
unnamed: C10.1, U3.4 (V3P3)
unnamed: C9.1, U3.6 (VCC)
unnamed: R11.1, U4.7 (ISET)
unnamed: C11.1, U4.4 (V3P3)
unnamed: C12.1, U4.6 (VCC)
unnamed: R12.1, U5.7 (ISET)
unnamed: C13.1, U5.4 (V3P3)
unnamed: C14.1, U5.6 (VCC)
unnamed: R13.1, U6.7 (ISET)
unnamed: C15.1, U6.4 (V3P3)
unnamed: C16.1, U6.6 (VCC)
unnamed: R14.1, U7.7 (ISET)
unnamed: C17.1, U7.4 (V3P3)
unnamed: C18.1, U7.6 (VCC)
unnamed: R15.1, U8.13 (KEY0)
unnamed: R16.1, U8.12 (KEY1)
unnamed: R17.1, U8.11 (KEY2)
unnamed: R18.1, U8.10 (KEY3)
unnamed: R19.1, U8.9 (KEY4)
PCLK: R2.2, U1.44 (PE14)
R0: JP10.1 (A), U1.97 (PE0)
R1: J2.29, JP10.3 (B), U1.24 (PA2)
R2: J2.30, U1.23 (PA1)
R3: J2.31, JP4.2 (B), U1.77 (PA15)
R4: J2.32, U1.29 (PA5)
R5: J2.33, U1.68 (PA9)
SCL: J2.37, R29.2, U1.92 (PB6), U8.6 (SCL/OUT3)
SDA: J2.36, R30.2, U1.93 (PB7), U8.3 (SDA/OUT0)
SWCLK: J1.4 (SWCLK/TCK), J6.3, U1.76 (PA14)
SWDIO: J1.2 (SWDIO/TMS), J6.2, R3.2, U1.72 (PA13)
SWO: JP3.2 (B), U1.89 (PB3)
TFT_CS: J2.11, R1.2, U1.51 (PB12)
TFT_MOSI: J2.9, U1.54 (PB15)
TFT_RESET: J2.6, J2.38, U1.64 (PC7)
TFT_SCK: J2.10, U1.52 (PB13)
TOUCH_1: R19.2, VR1.6 (TOUCH)
TOUCH_2: R18.2, VR2.6 (TOUCH)
TOUCH_3: R17.2, VR3.6 (TOUCH)
TOUCH_4: R16.2, VR4.6 (TOUCH)
TOUCH_5: R15.2, VR5.6 (TOUCH)
TOUCH_INT: R28.2, U1.42 (PE12), U8.5 (~CHANGE/OUT4)
TP_IRQ: J2.35, U1.45 (PE15)
USB_D+: J3.A6 (D+), J3.B6 (D+), R9.2
USB_D-: J3.A7 (D-), J3.B7 (D-), R8.1
VSYNC: J2.14, U1.28 (PA4)
Vdrive: SW1.2 (B), U3.9 (VIN), U4.9 (VIN), U5.9 (VIN), U6.9 (VIN), U7.9 (VIN)
WIPER_1: U1.15 (PC0), VR1.5 (WIPER_1)
WIPER_2: U1.16 (PC1), VR2.5 (WIPER_1)
WIPER_3: U1.17 (PC2_C), VR3.5 (WIPER_1)
WIPER_4: U1.18 (PC3_C), VR4.5 (WIPER_1)
WIPER_5: U1.32 (PC4), VR5.5 (WIPER_1)
nRST: C30.1, J1.10 (~RESET), R25.2, SW2.1 (A), U1.14 (NRST)

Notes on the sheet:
DEBUG HEADER
CAPACITIVE SENSOR
MOTOR DRIVERS
TFT & BACKLIGHT
FADER TRACKS

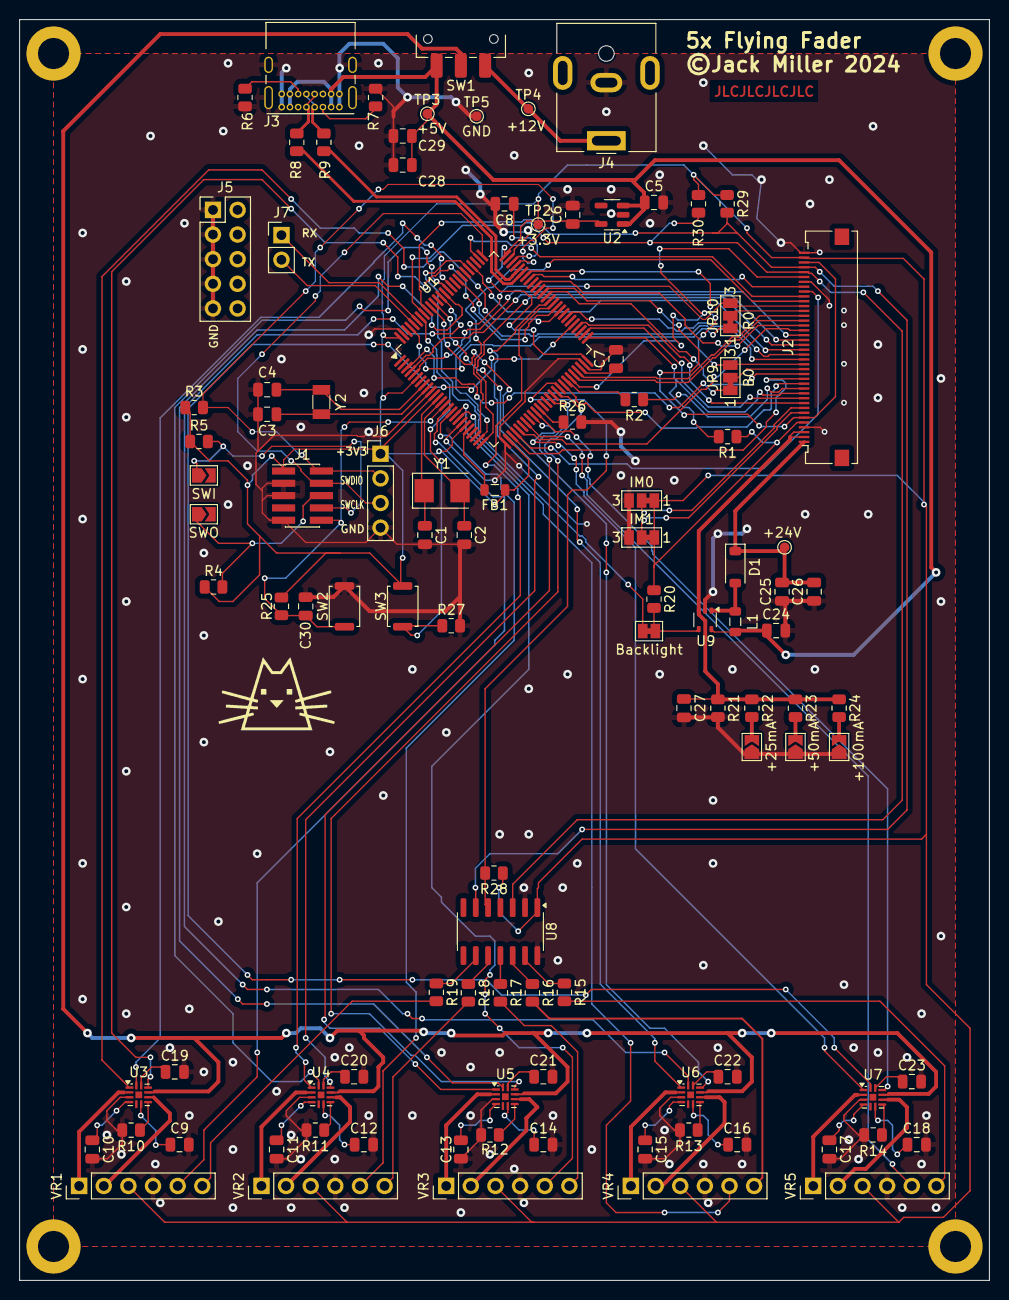
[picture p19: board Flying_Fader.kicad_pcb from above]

Board: 2 copper layers, 100.0 x 130.0 mm, 104 parts (0 on the bottom side), 136 nets.

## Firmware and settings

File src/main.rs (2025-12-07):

#![no_std]
#![no_main]

use defmt::{info, error, panic};
use embassy_executor::Spawner;
use embassy_stm32::{bind_interrupts, mode, usb, Config};
use embassy_stm32::adc::{Adc, SampleTime, Resolution};
use embassy_stm32::gpio::{Level, Output, OutputType, Speed};
use embassy_stm32::peripherals::{I2C1, TIM3, TIM4, USB_OTG_HS};
use embassy_stm32::time::{Hertz, khz};
use embassy_stm32::timer::{GeneralInstance4Channel, low_level::OutputPolarity};
use embassy_stm32::timer::simple_pwm::{PwmPin, SimplePwm};
use embassy_time::{Timer};
use embassy_stm32::i2c::{self, Error, I2c};

use embassy_futures::join::*;
use embassy_stm32::usb::{Driver, Instance, InterruptHandler};
use embassy_usb::driver::EndpointError;
use embassy_usb::Builder;
use embassy_usb::class::midi::MidiClass;

use pid::Pid;
use core::sync::atomic::{AtomicBool, AtomicU16, Ordering};
use embassy_usb::class::midi;
use {defmt_rtt as _, panic_probe as _};

const ADDRESS: u8 = 0x1B;
const HARDWARE_ID: u8 = 0x00;
const FIRMWARE_VERSION: u8 = 0x01;
const DETECTION_STATUS: u8 = 0x02;
const KEY_STATUS: u8 = 0x03;
const KEY_0_NTHR: u8 = 32;
const NTHR: u8 = 30;
// const KEY_5_NTHR: u8 = 37;
const KEY_0_AKS: u8 = 39;
const AKE_AKS: u8 = 0b100000_00; // 32 sample averaging, no adjacent key suppression
const MAX_ON_DURATION: u8 = 55;
const CALIBRATE: u8 = 56;

bind_interrupts!(struct Irqs {
    I2C1_EV => i2c::EventInterruptHandler<I2C1>;
    I2C1_ER => i2c::ErrorInterruptHandler<I2C1>;
    OTG_HS => InterruptHandler<USB_OTG_HS>;
});

pub fn clamp<T: PartialOrd>(input: T, min: T, max: T) -> T {
    if min < max { if input < min { min } else if input > max { max } else { input } }
    else { // case where you accidentally flipped min and max
        if input < max { min } else if input > min { max } else { input } }
}


static SLIDER_1_MEAS: AtomicU16 = AtomicU16::new(0);
static SLIDER_1_DES: AtomicU16 = AtomicU16::new(0);
static SLIDER_1_TOUCH: AtomicBool = AtomicBool::new(false);
static SLIDER_2_MEAS: AtomicU16 = AtomicU16::new(0);
static SLIDER_2_DES: AtomicU16 = AtomicU16::new(0);
static SLIDER_2_TOUCH: AtomicBool = AtomicBool::new(false);
static SLIDER_3_MEAS: AtomicU16 = AtomicU16::new(0);
static SLIDER_3_DES: AtomicU16 = AtomicU16::new(0);
static SLIDER_3_TOUCH: AtomicBool = AtomicBool::new(false);
static SLIDER_4_MEAS: AtomicU16 = AtomicU16::new(0);
static SLIDER_4_DES: AtomicU16 = AtomicU16::new(0);
static SLIDER_4_TOUCH: AtomicBool = AtomicBool::new(false);
static SLIDER_5_MEAS: AtomicU16 = AtomicU16::new(0);
static SLIDER_5_DES: AtomicU16 = AtomicU16::new(0);
static SLIDER_5_TOUCH: AtomicBool = AtomicBool::new(false);


#[embassy_executor::main]
async fn main(spawner: Spawner) {
    let mut config = Config::default();
    {
        use embassy_stm32::rcc::*;
        config.rcc.hsi = Some(HSIPrescaler::DIV1); // 64 MHz
        config.rcc.csi = false;
        config.rcc.hsi48 = Some(Hsi48Config { sync_from_usb: true }); // needed for USB
        config.rcc.pll1 = Some(Pll {
            source: PllSource::HSI,
            prediv: PllPreDiv::DIV4,
            mul: PllMul::MUL24,
            divp: Some(PllDiv::DIV2), // 192 MHz
            divq: Some(PllDiv::DIV2), // 192 MHz
            divr: None,
        });
        config.rcc.pll2 = Some(Pll {
            source: PllSource::HSI,
            prediv: PllPreDiv::DIV4,
            mul: PllMul::MUL8,
            divp: Some(PllDiv::DIV3), // 42.66667 MHz
            divq: None,
            divr: None,
        });
        config.rcc.pll3 = Some(Pll {
            source: PllSource::HSI,
            prediv: PllPreDiv::DIV4,
            mul: PllMul::MUL8,
            divp: Some(PllDiv::DIV2), // 64 MHz
            divq: None,
            divr: Some(PllDiv::DIV3), // 42.66667 MHZ
        });
        config.rcc.sys = Sysclk::PLL1_P; // 192 MHz
        config.rcc.ahb_pre = AHBPrescaler::DIV1; // 192 MHz
        config.rcc.apb1_pre = APBPrescaler::DIV2; // 96 MHz
        config.rcc.apb2_pre = APBPrescaler::DIV2; // 96 MHz
        config.rcc.apb3_pre = APBPrescaler::DIV2; // 96 MHz
        config.rcc.apb4_pre = APBPrescaler::DIV2; // 96 MHz
        config.rcc.voltage_scale = VoltageScale::Scale0;
        config.rcc.mux.usbsel = mux::Usbsel::HSI48;
    }
    
    let mut p = embassy_stm32::init(config);

    info!("Starting program...");

    // ADC Initialization
    let mut adc2 = Adc::new(p.ADC2);
    adc2.set_sample_time(SampleTime::CYCLES16_5);
    adc2.set_resolution(Resolution::BITS8);
    
    // Capacitive Touch Sensor Initialization
    let mut i2c_config = i2c::Config::default();
    i2c_config.frequency = Hertz(100_000);
    let mut i2c = I2c::new(
        p.I2C1,
        p.PB6,
        p.PB7,
        Irqs,
        p.DMA1_CH4,
        p.DMA1_CH5,
        i2c_config
    );

    let mut data = [0u8; 1];

    match i2c.write_read(ADDRESS, &[HARDWARE_ID], &mut data).await {
        Ok(()) => info!("Whoami: {:#01x}", data[0]),
        Err(Error::Timeout) => error!("Operation timed out"),
        Err(e) => error!("I2c Error: {:?}", e),
    }
    match i2c.write_read(ADDRESS, &[FIRMWARE_VERSION], &mut data).await {
        Ok(()) => info!("Firmware version: {:#01x}", data[0]),
        Err(Error::Timeout) => error!("Operation timed out"),
        Err(e) => error!("I2c Error: {:?}", e),
    }

    for i in 0..5 {
        match i2c.write(ADDRESS, &[KEY_0_AKS + i, AKE_AKS]).await {
            Ok(()) => info!("Set Key {} AKE/AKS", i),
            Err(Error::Timeout) => error!("Operation timed out"),
            Err(e) => error!("I2c Error: {:?}", e),
        }
    }

    match i2c.write(ADDRESS, &[MAX_ON_DURATION, 138]).await {
        Ok(()) => info!("Set Key Max on Duration to 22 seconds"),
        Err(Error::Timeout) => error!("Operation timed out"),
        Err(e) => error!("I2c Error: {:?}", e),
    }

    for i in 0..5 {
        match i2c.write(ADDRESS, &[KEY_0_NTHR+i, NTHR]).await {
            Ok(()) => info!("Set Key {} NTHR", i),
            Err(Error::Timeout) => error!("Operation timed out"),
            Err(e) => error!("I2c Error: {:?}", e),
        }
        /*let mut data = [0u8; 1];
        match i2c.write_read(ADDRESS, &[KEY_0_NTHR+i], &mut data).await {
            Ok(()) => info!("Key {} NTHR: {}", i, data[0]),
            Err(Error::Timeout) => error!("Operation timed out"),
            Err(e) => error!("I2c Error: {:?}", e),
        }*/
    }

    for _i in 0..1 {
        match i2c.write(ADDRESS, &[CALIBRATE, 5]).await {
            Ok(()) => info!("Started calibration"),
            Err(Error::Timeout) => error!("Operation timed out"),
            Err(e) => error!("I2c Error: {:?}", e),
        }

        loop {
            match i2c.write_read(ADDRESS, &[DETECTION_STATUS], &mut data).await {
                // Ok(()) => info!("Detection Status: {:#010b}", data[0]),
                Ok(()) => (),
                Err(Error::Timeout) => error!("Operation timed out"),
                Err(e) => error!("I2c Error: {:?}", e),
            }
            let calibration = ((1 << 7) & data[0]) > 0;
            if !calibration {
                info!("Calibration finished");
                break;
            } else {
                info!("Calibration not finished");
                Timer::after_millis(50).await;
            }
        }
    }

    // LCD initialization
    let lcd_backlight = p.PC12;
    let lcd_backlight_channel = PwmPin::new(lcd_backlight, OutputType::PushPull);
    let mut lcd_backlight_pwm = SimplePwm::new(p.TIM15, Some(lcd_backlight_channel), None, None, None, khz(50), Default::default());

    let backlight_duty = 50_u8;
    lcd_backlight_pwm.ch1().set_duty_cycle_percent(backlight_duty);
    
    // Motor initialization
    let mot1_sleep = p.PD4;
    let mot1_in1 = p.PD12;
    let mot1_in2 = p.PD13;
    let mot2_sleep = p.PD5;
    let mot2_in1 = p.PD14;
    let mot2_in2 = p.PD15;
    let mot3_sleep = p.PD6;
    let mot3_in1 = p.PE9;
    let mot3_in2 = p.PE11;
    let mot4_sleep = p.PD7;
    let mot4_in1 = p.PB4;
    let mot4_in2 = p.PB5;
    let mot5_sleep = p.PD8;
    let mot5_in1 = p.PB0;
    let mot5_in2 = p.PB1;

    let mut sleep1 = Output::new(mot1_sleep, Level::High, Speed::Low);
    let mut sleep2 = Output::new(mot2_sleep, Level::High, Speed::Low);
    let mut sleep3 = Output::new(mot3_sleep, Level::High, Speed::Low);
    let mut sleep4 = Output::new(mot4_sleep, Level::High, Speed::Low);
    let mut sleep5 = Output::new(mot5_sleep, Level::High, Speed::Low);
    sleep1.set_high();
    sleep2.set_high();
    sleep3.set_high();
    sleep4.set_high();
    sleep5.set_high();

    let mot1_ch1 = PwmPin::new(mot1_in1, OutputType::PushPull);
    let mot1_ch2 = PwmPin::new(mot1_in2, OutputType::PushPull);
    let mut mot1_pwm = SimplePwm::new(p.TIM4, Some(mot1_ch1), Some(mot1_ch2), None, None, khz(20), Default::default());
    let mot2_ch1 = PwmPin::new(mot2_in1, OutputType::PushPull);
    let mot2_ch2 = PwmPin::new(mot2_in2, OutputType::PushPull);
    let mut mot2_pwm = SimplePwm::new(unsafe {TIM4::steal()}, None, None, Some(mot2_ch1), Some(mot2_ch2), khz(20), Default::default());
    let mot3_ch1 = PwmPin::new(mot3_in1, OutputType::PushPull);
    let mot3_ch2 = PwmPin::new(mot3_in2, OutputType::PushPull);
    let mut mot3_pwm = SimplePwm::new(p.TIM1, Some(mot3_ch1), Some(mot3_ch2), None, None, khz(20), Default::default());
    let mot4_ch1 = PwmPin::new(mot4_in1, OutputType::PushPull);
    let mot4_ch2 = PwmPin::new(mot4_in2, OutputType::PushPull);
    let mut mot4_pwm = SimplePwm::new(p.TIM3, Some(mot4_ch1), Some(mot4_ch2), None, None, khz(20), Default::default());
    let mot5_ch1 = PwmPin::new(mot5_in1, OutputType::PushPull);
    let mot5_ch2 = PwmPin::new(mot5_in2, OutputType::PushPull);
    let mut mot5_pwm = SimplePwm::new(unsafe {TIM3::steal()}, None, None, Some(mot5_ch1), Some(mot5_ch2), khz(20), Default::default());

    mot1_pwm.ch1().set_polarity(OutputPolarity::ActiveLow); // inverted PWM
    mot1_pwm.ch2().set_polarity(OutputPolarity::ActiveLow);
    mot2_pwm.ch3().set_polarity(OutputPolarity::ActiveLow);
    mot2_pwm.ch4().set_polarity(OutputPolarity::ActiveLow);
    mot3_pwm.ch1().set_polarity(OutputPolarity::ActiveLow);
    mot3_pwm.ch2().set_polarity(OutputPolarity::ActiveLow);
    mot4_pwm.ch1().set_polarity(OutputPolarity::ActiveLow);
    mot4_pwm.ch2().set_polarity(OutputPolarity::ActiveLow);
    mot5_pwm.ch3().set_polarity(OutputPolarity::ActiveLow);
    mot5_pwm.ch4().set_polarity(OutputPolarity::ActiveLow);

    enable_motor(&mut mot1_pwm, 'a');
    enable_motor(&mut mot2_pwm, 'b');
    enable_motor(&mut mot3_pwm, 'a');
    enable_motor(&mut mot4_pwm, 'a');
    enable_motor(&mut mot5_pwm, 'b');

    let desired_position1 = SLIDER_1_DES.load(Ordering::Relaxed);
    let desired_position2 = SLIDER_2_DES.load(Ordering::Relaxed);
    let desired_position3 = SLIDER_3_DES.load(Ordering::Relaxed);
    let desired_position4 = SLIDER_4_DES.load(Ordering::Relaxed);
    let desired_position5 = SLIDER_5_DES.load(Ordering::Relaxed);
    
    let mut pid1 = Pid::new(desired_position1 as f32, 100_f32);
    let mut pid2 = Pid::new(desired_position2 as f32, 100_f32);
    let mut pid3 = Pid::new(desired_position3 as f32, 100_f32);
    let mut pid4 = Pid::new(desired_position4 as f32, 100_f32);
    let mut pid5 = Pid::new(desired_position5 as f32, 100_f32);

    let pid_p = 0.85; // 0.75
    let pid_p_lim = 100_f32;
    let pid_i = 1.7;
    let pid_i_lim = 25_f32;
    let pid_d = 0.0;
    let pid_d_lim = 0_f32;
    pid1.p(pid_p, pid_p_lim);
    pid1.i(pid_i, pid_i_lim);
    pid1.d(pid_d, pid_d_lim);
    pid2.p(pid_p, pid_p_lim);
    pid2.i(pid_i, pid_i_lim);
    pid2.d(pid_d, pid_d_lim);
    pid3.p(pid_p, pid_p_lim);
    pid3.i(pid_i, pid_i_lim);
    pid3.d(pid_d, pid_d_lim);
    pid4.p(pid_p, pid_p_lim);
    pid4.i(pid_i, pid_i_lim);
    pid4.d(pid_d, pid_d_lim);
    pid5.p(pid_p, pid_p_lim);
    pid5.i(pid_i, pid_i_lim);
    pid5.d(pid_d, pid_d_lim);
    
    spawner.spawn(get_touch(i2c, sleep1, sleep2, sleep3, sleep4, sleep5)).unwrap();


    // USB Initialization
    let mut ep_out_buffer = [0u8; 256];
    let mut config = usb::Config::default();
    config.vbus_detection = false; // Necessary since STM32 is powered solely by USB
    let driver = Driver::new_fs(p.USB_OTG_HS, Irqs, p.PA12, p.PA11, &mut ep_out_buffer, config);
    // Create embassy-usb Config
    let mut config = embassy_usb::Config::new(0xc0de, 0xcafe);
    config.manufacturer = Some("CollapseOfSound");
    config.product = Some("Flying Fader");
    config.serial_number = Some("00000001");
    config.max_power = 200;
    config.max_packet_size_0 = 64;
    // Required for windows compatibility.
    // https://developer.nordicsemi.com/nRF_Connect_SDK/doc/1.9.1/kconfig/CONFIG_CDC_ACM_IAD.html#help
    config.device_class = 0xEF;
    config.device_sub_class = 0x02;
    config.device_protocol = 0x01;
    config.composite_with_iads = true;
    // Create embassy-usb DeviceBuilder using the driver and config.
    // It needs some buffers for building the descriptors.
    let mut config_descriptor = [0; 256];
    let mut bos_descriptor = [0; 256];
    let mut control_buf = [0; 64];
    let mut builder = Builder::new(
        driver,
        config,
        &mut config_descriptor,
        &mut bos_descriptor,
        &mut [], // no msos descriptors
        &mut control_buf,
    );
    let class = MidiClass::new(&mut builder, 1, 1, 64);
    // The `MidiClass` can be split into `Sender` and `Receiver`, to be used in separate tasks.
    let (mut sender, mut receiver) = class.split();
    let mut usb = builder.build();
    let usb_fut = usb.run();

    // Use the Midi class!
    let midi_send_fut = async {
        loop {
            sender.wait_connection().await;
            info!("Connected");
            let _ = midi_send(&mut sender).await;
            info!("Disconnected");
        }
    };
    
    let midi_recv_fut = async {
        loop {
            receiver.wait_connection().await;
            // info!("Connected");
            let _ = midi_recv(&mut receiver).await;
            // info!("Disconnected");
        }
    };

    let slider_fut = async {
        loop {
            let mot1_measured = adc2.blocking_read(&mut p.PC0) >> 1;
            let mot2_measured = adc2.blocking_read(&mut p.PC1) >> 1;// was adc2.read
            let mot3_measured = adc2.blocking_read(&mut p.PC2_C) >> 1;
            let mot4_measured = adc2.blocking_read(&mut p.PC3_C) >> 1;
            let mot5_measured = adc2.blocking_read(&mut p.PC4) >> 1;
            // info!("measured: {}, {}, {}, {}, {}", mot1_measured, mot2_measured, mot3_measured, mot4_measured, mot5_measured);
            
            SLIDER_1_MEAS.store(mot1_measured, Ordering::Relaxed);
            if SLIDER_1_TOUCH.load(Ordering::Relaxed) { SLIDER_1_DES.store(mot1_measured, Ordering::Relaxed); }
            SLIDER_2_MEAS.store(mot2_measured, Ordering::Relaxed);
            if SLIDER_2_TOUCH.load(Ordering::Relaxed) { SLIDER_2_DES.store(mot2_measured, Ordering::Relaxed); }
            SLIDER_3_MEAS.store(mot3_measured, Ordering::Relaxed);
            if SLIDER_3_TOUCH.load(Ordering::Relaxed) { SLIDER_3_DES.store(mot3_measured, Ordering::Relaxed); }
            SLIDER_4_MEAS.store(mot4_measured, Ordering::Relaxed);
            if SLIDER_4_TOUCH.load(Ordering::Relaxed) { SLIDER_4_DES.store(mot4_measured, Ordering::Relaxed); }
            SLIDER_5_MEAS.store(mot5_measured, Ordering::Relaxed);
            if SLIDER_5_TOUCH.load(Ordering::Relaxed) { SLIDER_5_DES.store(mot5_measured, Ordering::Relaxed); }

            pid1.setpoint(SLIDER_1_DES.load(Ordering::Relaxed) as f32);
            let output1 = pid1.next_control_output(mot1_measured as f32);
            let mut correction1 = output1.output as i16;
            if correction1.abs() > 5_i16 { correction1 += 20_i16 * correction1.signum(); }
            set_motor_duty(&mut mot1_pwm, 'a', correction1);
            
            pid2.setpoint(SLIDER_2_DES.load(Ordering::Relaxed) as f32);
            let output2 = pid2.next_control_output(mot2_measured as f32);
            let mut correction2 = output2.output as i16;
            if correction2.abs() > 5_i16 { correction2 += 20_i16 * correction2.signum(); }
            set_motor_duty(&mut mot2_pwm, 'b', correction2);
            
            pid3.setpoint(SLIDER_3_DES.load(Ordering::Relaxed) as f32);
            let output3 = pid3.next_control_output(mot3_measured as f32);
            let mut correction3 = output3.output as i16;
            if correction3.abs() > 5_i16 { correction3 += 20_i16 * correction3.signum(); }
            set_motor_duty(&mut mot3_pwm, 'a', correction3);
            
            pid4.setpoint(SLIDER_4_DES.load(Ordering::Relaxed) as f32);
            let output4 = pid4.next_control_output(mot4_measured as f32);
            let mut correction4 = output4.output as i16;
            if correction4.abs() > 5_i16 { correction4 += 20_i16 * correction4.signum(); }
            set_motor_duty(&mut mot4_pwm, 'a', correction4);
            
            pid5.setpoint(SLIDER_5_DES.load(Ordering::Relaxed) as f32);
            let output5 = pid5.next_control_output(mot5_measured as f32);
            let mut correction5 = output5.output as i16;
            if correction5.abs() > 5_i16 { correction5 += 20_i16 * correction5.signum(); }
            set_motor_duty(&mut mot5_pwm, 'b', correction5);

            // info!("Setpoint: {}, {}, {}, {}, {}", pid1.setpoint, pid2.setpoint, pid3.setpoint, pid4.setpoint, pid5.setpoint);
            // info!("Correction: {}, {}, {}, {}, {}", correction1, correction2, correction3, correction4, correction5);

            Timer::after_millis(35).await;
        }
    };

    // Run everything concurrently.
    // If we had made everything `'static` above instead, we could do this using separate tasks instead.
    join4(usb_fut, midi_send_fut, midi_recv_fut, slider_fut).await;
}

/// Empty struct for USB disconnection handling
struct Disconnected {}

/// Convert EndpointError to Disconnected
impl From<EndpointError> for Disconnected {
    fn from(val: EndpointError) -> Self {
        match val {
            EndpointError::BufferOverflow => panic!("Buffer overflow"),
            EndpointError::Disabled => Disconnected {},
        }
    }
}
/// Output MIDI CC signals over USB
async fn midi_recv<'d, T: Instance + 'd>(class: &mut midi::Receiver<'d, Driver<'d, T>>) -> Result<(), Disconnected> {
    let mut buf = [0; 64];
    loop {
        let n = class.read_packet(&mut buf).await?;
        let data = &buf[..n];
        // info!("data: {:x}", data);
        // info!("channel: {}", data[2]);
        
        if data[0] == 0xb && data[1] == 0xb0 { // Cable 0, B for control change
            for i in (0..n).step_by(4) {
                // info!("data[{}]: {:x}, {:x}, {:x}, {:x}", i, data[i], data[i+1], data[i+2], data[i+3]);
                if data[i+2] == 16 { SLIDER_1_DES.store(data[i+3] as u16, Ordering::Relaxed); } // Decimal channel 16
                if data[i+2] == 17 { SLIDER_2_DES.store(data[i+3] as u16, Ordering::Relaxed); } // Decimal channel 17
                if data[i+2] == 18 { SLIDER_3_DES.store(data[i+3] as u16, Ordering::Relaxed); } // Decimal channel 18
                if data[i+2] == 19 { SLIDER_4_DES.store(data[i+3] as u16, Ordering::Relaxed); } // Decimal channel 19
                if data[i+2] == 80 { SLIDER_5_DES.store(data[i+3] as u16, Ordering::Relaxed); } // Decimal channel 80
            }
        }
    }
}

/// Receive MIDI CC signals over USB
async fn midi_send<'d, T: Instance + 'd>(class: &mut midi::Sender<'d, Driver<'d, T>>) -> Result<(), Disconnected> {
    let mut previous_position1: u8 = 0;
    let mut previous_position2: u8 = 0;
    let mut previous_position3: u8 = 0;
    let mut previous_position4: u8 = 0;
    let mut previous_position5: u8 = 0;
    
    loop {
        let slider_position1 = clamp(SLIDER_1_MEAS.load(Ordering::Relaxed), 0, 127) as u8;
        if (previous_position1 != slider_position1) && (SLIDER_1_TOUCH.load(Ordering::Relaxed)) {
            class.write_packet(&[0x0b, 0xb0, 16, slider_position1]).await?; // First byte is cable 0, B for control change
            previous_position1 = slider_position1;
        }
        let slider_position2 = clamp(SLIDER_2_MEAS.load(Ordering::Relaxed), 0, 127) as u8;
        if (previous_position2 != slider_position2) && (SLIDER_2_TOUCH.load(Ordering::Relaxed)) {
            class.write_packet(&[0x0b, 0xb0, 17, slider_position2]).await?; // First byte is cable 0, B for control change
            previous_position2 = slider_position2;
        }
        let slider_position3 = clamp(SLIDER_3_MEAS.load(Ordering::Relaxed), 0, 127) as u8;
        if (previous_position3 != slider_position3) && (SLIDER_3_TOUCH.load(Ordering::Relaxed)) {
            class.write_packet(&[0x0b, 0xb0, 18, slider_position3]).await?; // First byte is cable 0, B for control change
            previous_position3 = slider_position3;
        }
        let slider_position4 = clamp(SLIDER_4_MEAS.load(Ordering::Relaxed), 0, 127) as u8;
        if (previous_position4 != slider_position4) && (SLIDER_4_TOUCH.load(Ordering::Relaxed)) {
            class.write_packet(&[0x0b, 0xb0, 19, slider_position4]).await?; // First byte is cable 0, B for control change
            previous_position4 = slider_position4;
        }
        let slider_position5 = clamp(SLIDER_5_MEAS.load(Ordering::Relaxed),0, 127) as u8;
        if (previous_position5 != slider_position5) && (SLIDER_5_TOUCH.load(Ordering::Relaxed)) {
            class.write_packet(&[0x0b, 0xb0, 80, slider_position5]).await?; // First byte is cable 0, B for control change
            previous_position5 = slider_position5;
        }
        
        Timer::after_millis(20).await;
    }
}
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

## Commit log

2024-06-11 Correct capacitive touch sensitivity
    [main.rs]
2024-06-14 Add CAD files (PCB & 3D)
    [2024-05-20T173932.xlsx, EDI2CAP.CFG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]
2024-06-15 Add CAD photo
2024-06-15 Add a sample song using Ableton Live

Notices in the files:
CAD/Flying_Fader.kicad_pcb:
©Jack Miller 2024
